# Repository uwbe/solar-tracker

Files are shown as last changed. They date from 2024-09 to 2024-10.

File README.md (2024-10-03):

# SolarTracker from Zachi Zolar
## Introduction
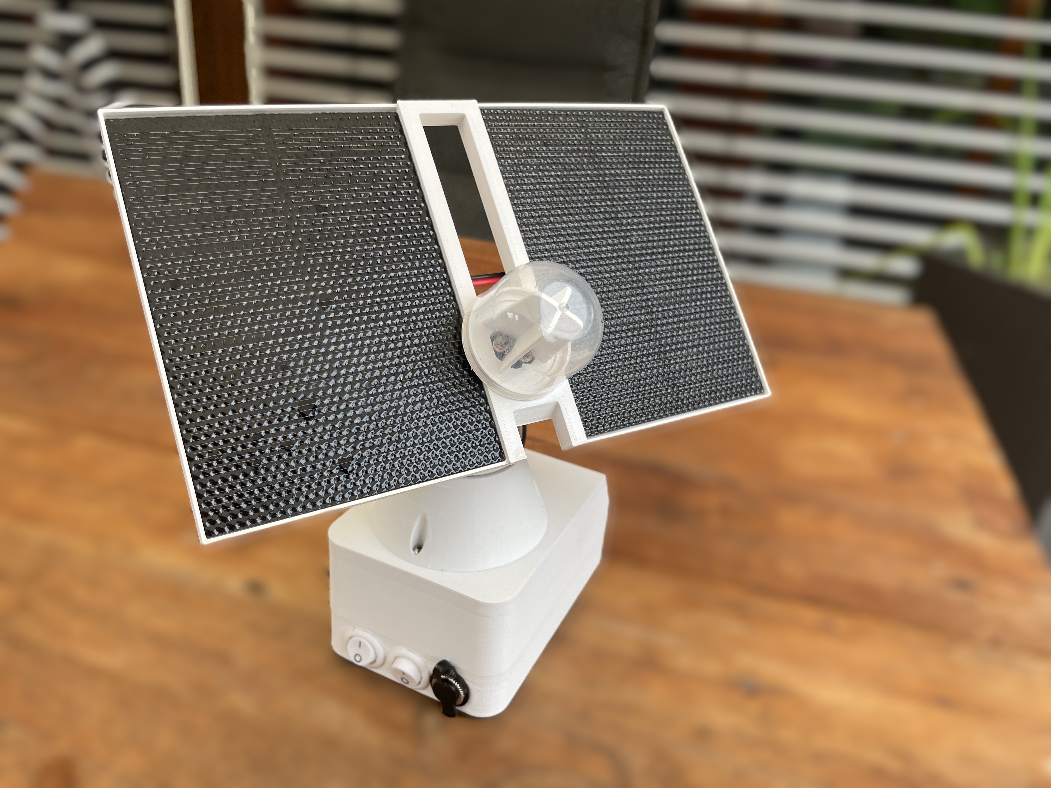
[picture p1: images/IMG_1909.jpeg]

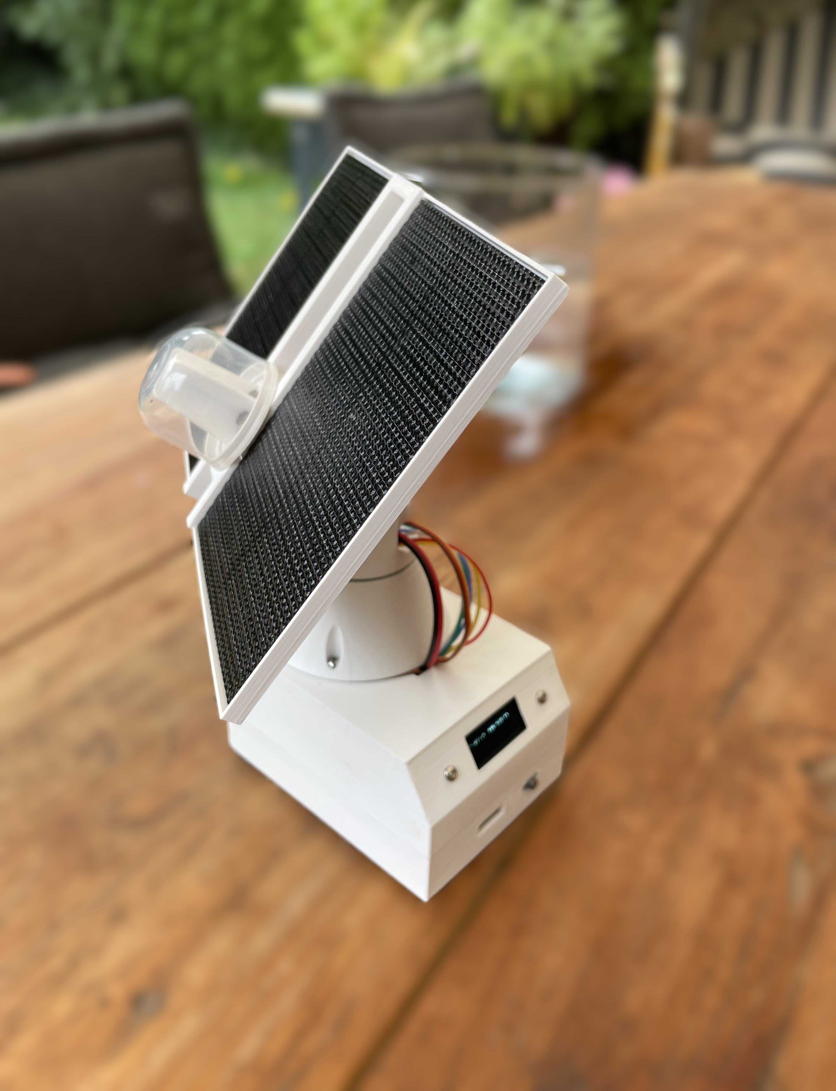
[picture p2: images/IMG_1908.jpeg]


This repository contains all necessary information to rebuilt a little solar tracker with 2x1W solar panels, which produces enough power to drive itself and, if the sun light is bright enough, a little garden fontain (1.4W).
The project is supposed as a starting point for Arduino enthusiast to create a funny little device and learn to bring all skills together, such as: 
* Programming Arduino Nano
* CAD
* PCB's and soldering
* 3D printing
* crimping wires and connections
* to overcome frustration
* to learn to pursue a goal patiently and persistently

The SolarTracker v1.0 from Zachi Zolar is far away from being ready. E.g. the first version was melting in the sun because it was 3D printed with PLA. This version printed with ASA withstands UV light and heat, 
but it is not really water protected.
Happy assembling!

A little [introduction](https://www.youtube.com/watch?v=XpIjK1iY8B4&t=24s) video in German on Youtube.

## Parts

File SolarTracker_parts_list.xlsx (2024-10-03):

Part | Amount | Example Order
Arduino Nano | 1 | https://de.aliexpress.com/item/1005005967644175.html
JST 2,54 15pin male | 2 | https://de.aliexpress.com/item/1005005258694395.html?scm_id=1007.40050.354490.0&scm-url=1007.40050.354490.0
JST 2,54 15pin female | 2 | https://de.aliexpress.com/item/4001198421663.html
Oled Display 0.91" | 1 | https://de.aliexpress.com/item/1005006365875553.html
Resistor 10k | 4 | https://de.aliexpress.com/item/32315929780.html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
photo resitor (LDR) | 4 | https://de.aliexpress.com/item/1005005968714360.html
Switch on/off | 2 | https://de.aliexpress.com/item/4000904999665.html
Clinch socket | 1 | https://de.aliexpress.com/item/1005005191616601.html
Clinch plug | 1 | https://de.aliexpress.com/item/1005001689451761.html
Servo SG90 | 2 | https://de.aliexpress.com/item/1005006283358420.html
Solar-Panel 1W | 2 | https://www.amazon.de/dp/B0BJPXJ61X?ref=ppx_yo2ov_dt_b_fed_asin_title
Dupont angled 90° 5pin | 1 | https://de.aliexpress.com/item/1005006438592096.html
Dupont pin header male 7pin | 1
Dupont pin header male 4pin | 1
Dupont pin header male 2pin | 1
INA219 | 1 | https://de.aliexpress.com/item/32377617416.html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
Akku 3.7V 14500 | 1 | https://de.aliexpress.com/item/1005004570483188.html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
Solar-Power Manager Waveshare SKU: 16120 | 1 | https://de.aliexpress.com/item/1005007342760815.html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
Brass Embedment Knurled Nut Heat Set | 1 | https://de.aliexpress.com/item/1005006359548769.html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
Stainless Steel Precision Ball set | 1 | https://de.aliexpress.com/item/1005005478220120.html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
JST Female Housing 4pins | 1 | https://www.amazon.de/dp/B0BHT1FQGY?ref=ppx_yo2ov_dt_b_fed_asin_title
Mini garden fontain max. 2.5 W | 1 | https://www.amazon.de/dp/B09V7RVX99?ref=ppx_yo2ov_dt_b_fed_asin_title
laboratory circuit board | 2 | https://de.aliexpress.com/item/1005007538599139.html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
3D printed parts from the STL directory | 10
PCB's as described in fritzing (or laboratory circuit boards) | 2
M3 and M2.5 Screws | various | https://www.amazon.de/dp/B0BQ7GGZ9M?ref=ppx_yo2ov_dt_b_fed_asin_title
Wires |  | https://www.amazon.de/dp/B098JKC4HW?ref=ppx_yo2ov_dt_b_fed_asin_title
ASA Filament | 1 | https://www.amazon.de/dp/B0C5H7S96Y?ref=ppx_yo2ov_dt_b_fed_asin_title
cover cap of Rituals of Hammam | 1 | https://www.amazon.de/RITUALS-Duschschaum-Vorteilspaket-Das-Ritual-Hammam/dp/B0CL4SBDPQ?hvadid=696322103951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
Aihasd 30 Stück Screw Terminal Leiterplatten-Anschlussklemme Block 5.08mm 2 Pin Pitch Klemme Printklemme 300V 16A | 1 | https://www.amazon.de/dp/B00VGGFPZW?ref=ppx_yo2ov_dt_b_fed_asin_title

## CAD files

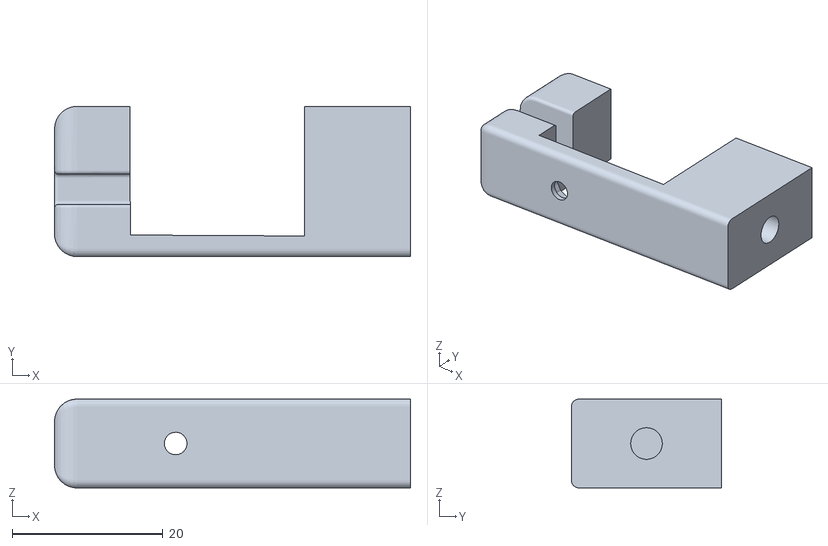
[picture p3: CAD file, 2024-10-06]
stl/solar_arm_big_sg90.stl
47.3 x 19.9 x 11.8

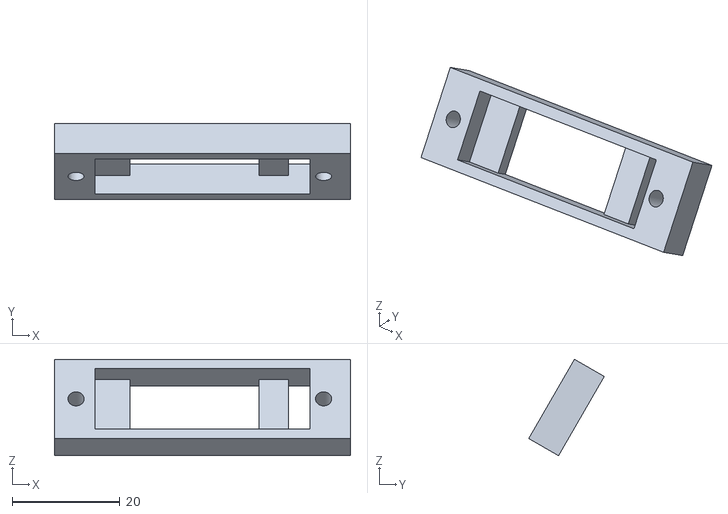
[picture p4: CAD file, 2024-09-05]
stl/solar_display.stl
55.0 x 14.0 x 17.9

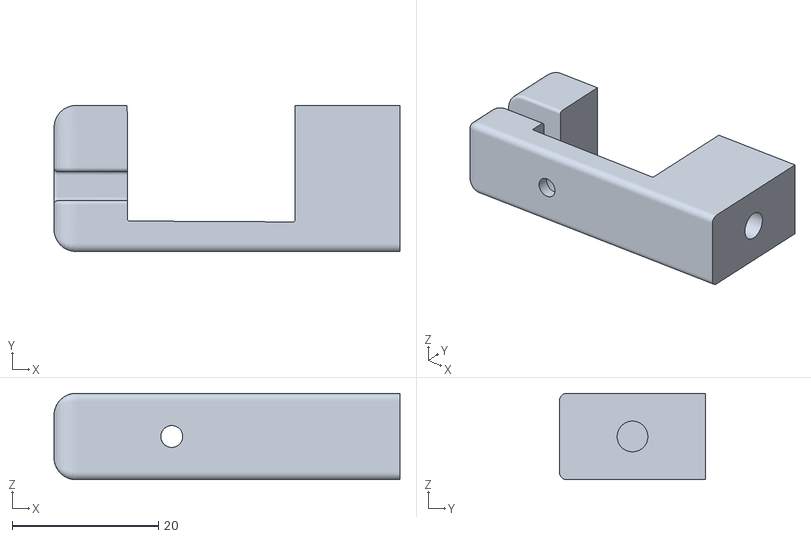
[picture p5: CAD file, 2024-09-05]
stl/solar_arm.stl
47.3 x 19.9 x 11.8

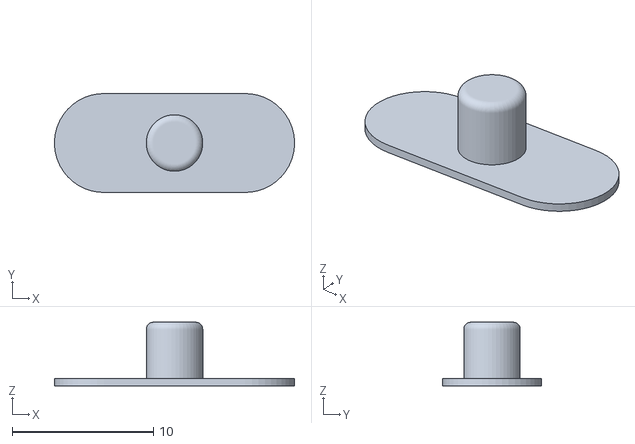
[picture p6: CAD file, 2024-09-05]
stl/solar_switch_cover.stl
17.0 x 7.00 x 4.50

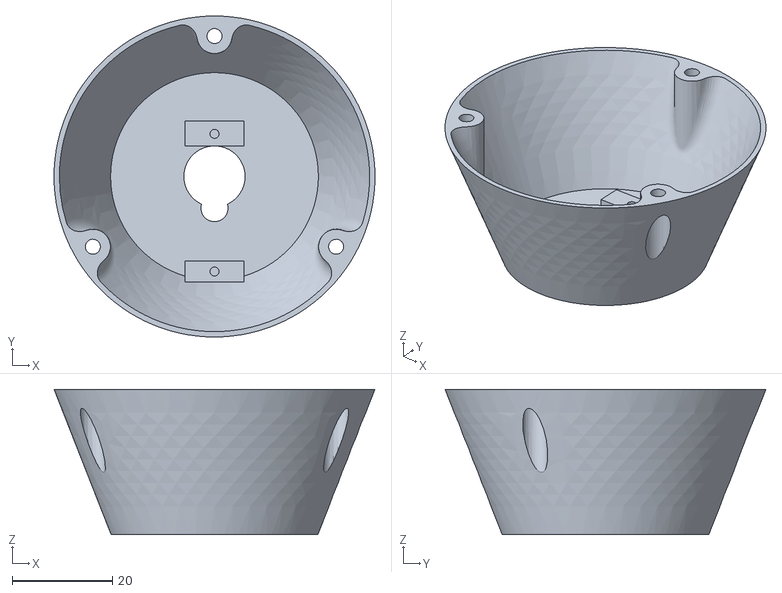
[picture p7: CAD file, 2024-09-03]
stl/solar_cone_base.stl
64.0 x 64.0 x 29.0

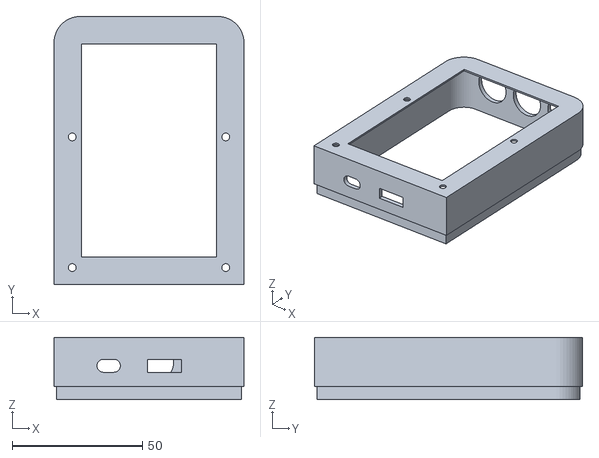
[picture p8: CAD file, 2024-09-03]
stl/solar_power_pack_v2.stl
73.0 x 103.0 x 24.0

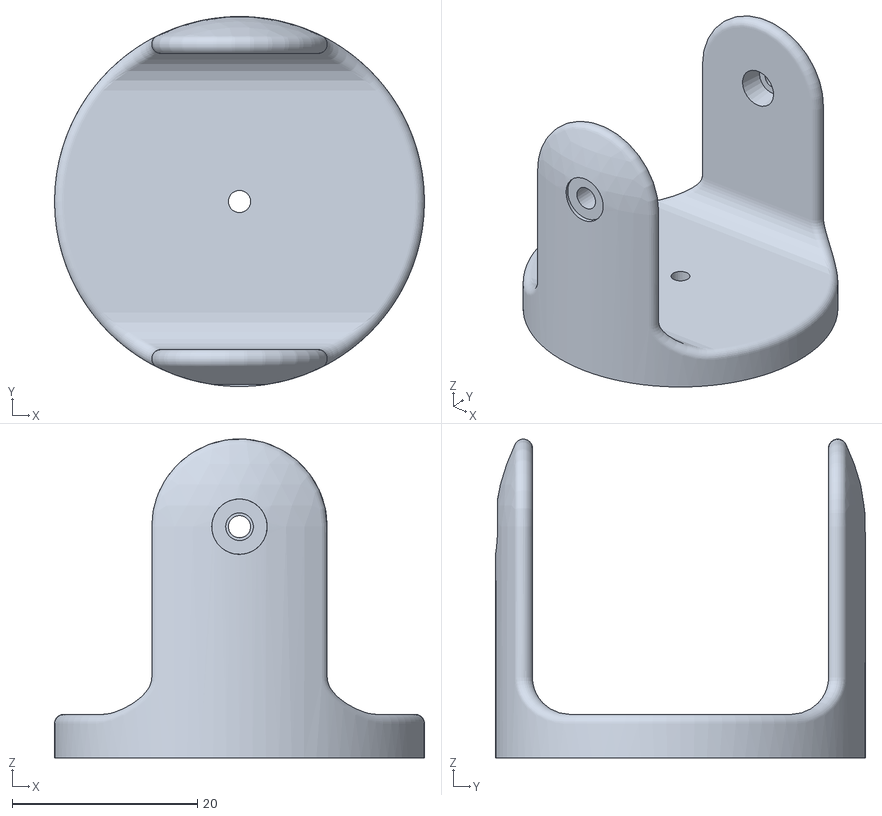
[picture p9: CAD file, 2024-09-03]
stl/solar_head.stl
40.0 x 40.0 x 34.5

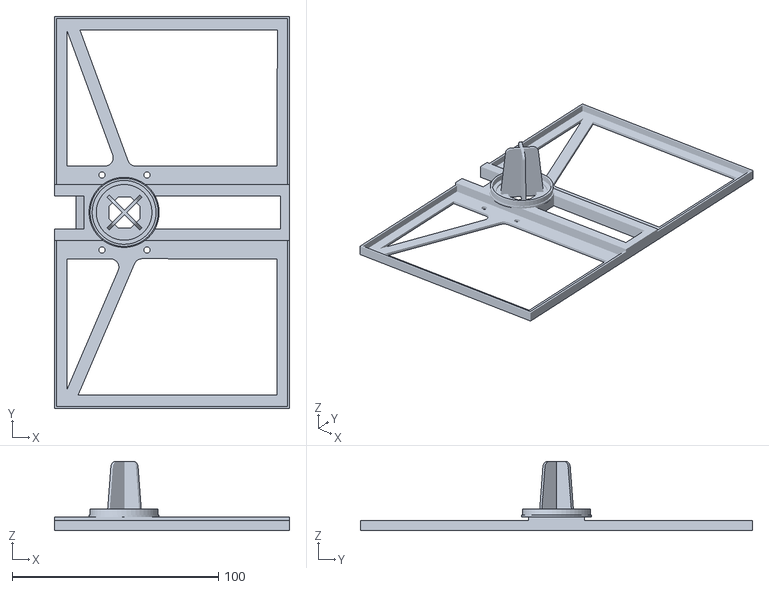
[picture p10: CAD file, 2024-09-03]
stl/solar_ldr_2W_panel.stl
113.8 x 190.0 x 33.5

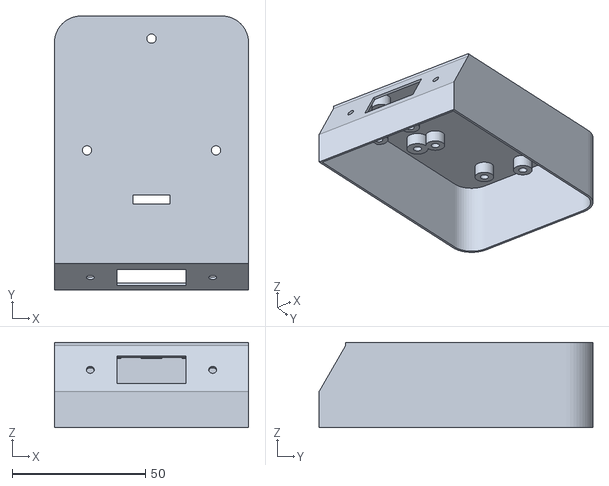
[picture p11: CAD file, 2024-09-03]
stl/solar_body_v2.stl
73.0 x 103.0 x 32.0

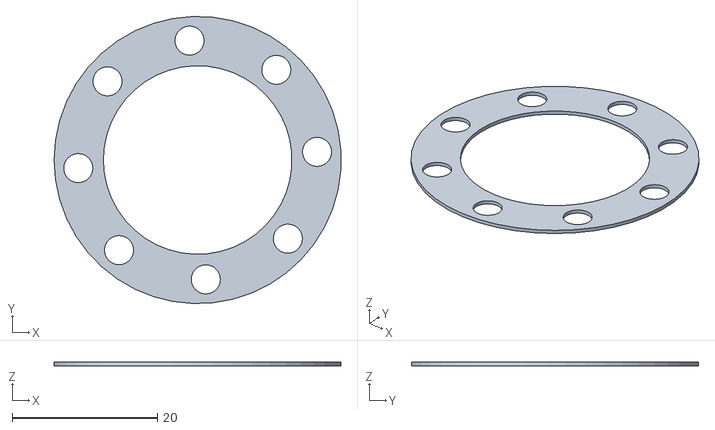
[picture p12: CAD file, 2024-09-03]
stl/solar_bearing.stl
39.6 x 39.6 x 0.5

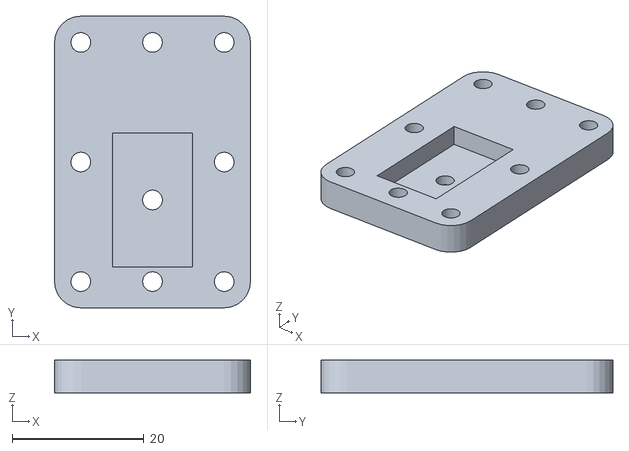
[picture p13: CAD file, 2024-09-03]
stl/solar_support.stl
29.8 x 44.4 x 5.00

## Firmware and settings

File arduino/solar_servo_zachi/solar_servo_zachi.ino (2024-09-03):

#include <Servo.h>
#include <Wire.h>
#include <Adafruit_GFX.h>
#include <Adafruit_SSD1306.h>
#include <Adafruit_INA219.h>

//0x31
#define OLED_RESET -1
#define SCREEN_WIDTH 128 // OLED display width, in pixels
#define SCREEN_HEIGHT 32 // OLED display height, in pixels
Adafruit_SSD1306 display(OLED_RESET);
bool invert = true;

Adafruit_INA219 ina219;

Servo horizontal; // horizontal servo
int servoh = 90;
int servohLimitHigh = 180;
int servohLimitLow = 0;

Servo vertical; // vertical servo
int servov = 45;
int servovLimitHigh = 95;
int servovLimitLow = 0;

// LDR pin connections
// name = analogpin;
int ldrtop = A0; //LDR top
int ldrright = A3; //LDR rigt
int ldrbottom = A1; //LDR bottom
int ldrleft = A2; //LDR left
int tolerance = 10;
int top = 0;
int bottom = 0;
int left = 0;
int right = 0;

int xpos = 89;
int dir = -1;

bool isSleepMode = false;
unsigned long startMillis;  
long currentAvg = 0;

//INA219 variables
float shuntvoltage = 0;
  float busvoltage = 0;
  float current_mA = 0;
  float loadvoltage = 0;
  float power_mW = 0;

static const unsigned char PROGMEM sun [] = {
0x80, 0x00, 0x00, 0x00, 0x00, 0x00, 0x00, 0x00, 0x43, 0xFF, 0xFF, 0xFF, 0xFF, 0xFF, 0xFF, 0x80,
0x40, 0x00, 0x00, 0x00, 0x00, 0x00, 0x00, 0x00, 0x80, 0x00, 0x00, 0x00, 0x00, 0x00, 0x00, 0x00,
0x40, 0x00, 0x00, 0x00, 0x00, 0x00, 0x00, 0x00, 0x80, 0x00, 0x00, 0x00, 0x00, 0x00, 0x00, 0x00,
0x20, 0x00, 0x00, 0x00, 0x00, 0x00, 0x00, 0x01, 0x02, 0x00, 0x00, 0x00, 0x00, 0x00, 0x00, 0x00,
0x20, 0x00, 0x00, 0x00, 0x00, 0x00, 0x00, 0x01, 0x01, 0xE0, 0x00, 0x00, 0x00, 0x00, 0x00, 0x00,
0x10, 0x00, 0x00, 0x00, 0x00, 0x00, 0x00, 0x02, 0x00, 0x1E, 0x00, 0x00, 0x00, 0x00, 0x00, 0x00,
0x08, 0x00, 0x00, 0x00, 0x00, 0x00, 0x00, 0x04, 0x00, 0x01, 0xE0, 0x00, 0x00, 0x00, 0x00, 0x00,
0x04, 0x00, 0x00, 0x00, 0x00, 0x00, 0x00, 0x08, 0x00, 0x00, 0x1C, 0x00, 0x00, 0x00, 0x00, 0x00,
0x02, 0x00, 0x00, 0x00, 0x00, 0x00, 0x00, 0x10, 0x18, 0x00, 0x00, 0x00, 0x00, 0x00, 0x00, 0x00,
0x02, 0x00, 0x00, 0x00, 0x00, 0x00, 0x00, 0x10, 0x06, 0x00, 0x00, 0x00, 0x00, 0x00, 0x00, 0x00,
0x01, 0x80, 0x00, 0x00, 0x00, 0x00, 0x00, 0x60, 0x01, 0x80, 0x00, 0x00, 0x00, 0x00, 0x00, 0x00,
0x40, 0x40, 0x00, 0x00, 0x00, 0x00, 0x00, 0x80, 0x00, 0x40, 0x00, 0x00, 0x00, 0x00, 0x00, 0x00,
0x80, 0x20, 0x00, 0x00, 0x00, 0x00, 0x01, 0x00, 0x00, 0x30, 0x00, 0x00, 0x00, 0x00, 0x00, 0x00,
0x00, 0x10, 0x00, 0x00, 0x00, 0x00, 0x02, 0x00, 0x80, 0x0C, 0x00, 0x00, 0x00, 0x00, 0x00, 0x00,
0x00, 0x0C, 0x00, 0x00, 0x00, 0x00, 0x0C, 0x00, 0x40, 0x03, 0x00, 0x00, 0x00, 0x00, 0x00, 0x00,
0x00, 0x03, 0x00, 0x00, 0x00, 0x00, 0x30, 0x00, 0x20, 0x00, 0x80, 0x00, 0x00, 0x00, 0x00, 0x00,
0x02, 0x00, 0xC0, 0x00, 0x00, 0x00, 0xC0, 0x10, 0x10, 0x00, 0x60, 0x00, 0x00, 0x00, 0x00, 0x00,
0x04, 0x00, 0x30, 0x00, 0x00, 0x03, 0x00, 0x08, 0x08, 0x00, 0x18, 0x00, 0x00, 0x00, 0x00, 0x00,
0x04, 0x00, 0x0E, 0x00, 0x00, 0x1C, 0x00, 0x04, 0x04, 0x00, 0x06, 0x00, 0x00, 0x00, 0x00, 0x00,
0x08, 0x00, 0x01, 0xF0, 0x01, 0xE0, 0x01, 0x02, 0x02, 0x00, 0x01, 0x80, 0x00, 0x00, 0x00, 0x00,
0x10, 0x08, 0x00, 0x0F, 0xFE, 0x00, 0x01, 0x01, 0x01, 0x00, 0x00, 0x40, 0x00, 0x00, 0x00, 0x00,
0x20, 0x10, 0x00, 0x00, 0x00, 0x00, 0x00, 0x80, 0x80, 0x80, 0x00, 0x30, 0x00, 0x00, 0x00, 0x00,
0x40, 0x10, 0x40, 0x00, 0x00, 0x00, 0x00, 0x80, 0x00, 0x40, 0x00, 0x0C, 0x00, 0x00, 0x00, 0x00,
0x40, 0x20, 0x80, 0x00, 0x00, 0x00, 0x40, 0x40, 0x00, 0x20, 0x00, 0x03, 0x00, 0x00, 0x00, 0x00,
0x80, 0x40, 0x80, 0x40, 0x00, 0x80, 0x40, 0x20, 0x00, 0x10, 0x00, 0x00, 0x80, 0x00, 0x00, 0x00,
0x00, 0x01, 0x00, 0x80, 0x80, 0x40, 0x20, 0x20, 0x00, 0x08, 0x00, 0x00, 0x60, 0x00, 0x00, 0x00,
0x00, 0x01, 0x00, 0x80, 0x80, 0x40, 0x20, 0x10, 0x00, 0x04, 0x00, 0x00, 0x18, 0x00, 0x00, 0x00,
0x00, 0x02, 0x01, 0x00, 0x80, 0x40, 0x10, 0x10, 0x00, 0x02, 0x00, 0x00, 0x06, 0x00, 0x00, 0x00,
0x00, 0x04, 0x01, 0x00, 0x80, 0x20, 0x10, 0x08, 0x00, 0x01, 0x00, 0x00, 0x01, 0x00, 0x00, 0x00,
0x00, 0x04, 0x02, 0x00, 0x80, 0x20, 0x08, 0x04, 0x00, 0x00, 0x80, 0x00, 0x00, 0x00, 0x00, 0x00,
0x00, 0x08, 0x00, 0x00, 0x80, 0x20, 0x08, 0x04, 0x00, 0x00, 0x00, 0x00, 0x00, 0x00, 0x00, 0x00,
0x00, 0x10, 0x00, 0x00, 0x80, 0x10, 0x08, 0x02, 0x00, 0x00, 0x00, 0x00, 0x00, 0x00, 0x00, 0x00
};

static const unsigned char PROGMEM lupe_bmp[] = {
0x07, 0xc0, 0x00, 
0x18, 0x30, 0x00, 
0x20, 0x08, 0x00, 
0x40, 0x04, 0x00, 
0x40, 0x04, 0x00, 
0x80, 0x02, 0x00, 
0x80, 0x02, 0x00, 
0x80, 0x02, 0x00, 
0x80, 0x02, 0x00, 
0x80, 0x02, 0x00, 
0x40, 0x04, 0x00, 
0x40, 0x04, 0x00, 
0x20, 0x0c, 0x00, 
0x18, 0x3e, 0x00, 
0x07, 0xc7, 0x00, 
0x00, 0x03, 0x80, 
0x00, 0x01, 0xc0, 
0x00, 0x00, 0xe0, 
0x00, 0x00, 0x70, 
0x00, 0x00, 0x30
};

static const unsigned char PROGMEM dark [] = {
0x00, 0x00, 0x00, 0x00, 0x20, 0x00, 0x00, 0x00, 0x00, 0x00, 0x00, 0x00, 0x00, 0x00, 0x00, 0x00,
0x00, 0x40, 0x00, 0x00, 0x20, 0x00, 0x00, 0x00, 0x0F, 0x78, 0x00, 0x00, 0x03, 0xF1, 0xFC, 0x00,
0x00, 0x40, 0x00, 0x00, 0x50, 0x00, 0x00, 0x01, 0xF0, 0x84, 0x00, 0x3F, 0xFC, 0x0E, 0x03, 0x00,
0x00, 0xA0, 0x00, 0x00, 0xDC, 0x00, 0x00, 0x7E, 0x10, 0x06, 0xFF, 0x40, 0x30, 0x08, 0x00, 0x80,
0x00, 0xA0, 0x00, 0x07, 0x03, 0x00, 0x00, 0x80, 0x00, 0x07, 0x00, 0xC0, 0x00, 0x00, 0x00, 0xF0,
0x07, 0x1C, 0x00, 0x01, 0xDC, 0x00, 0x01, 0x00, 0x00, 0x08, 0x00, 0x00, 0x00, 0x00, 0x00, 0x08,
0x18, 0x03, 0x00, 0x00, 0x50, 0x00, 0x01, 0x00, 0x00, 0x10, 0x00, 0x00, 0x00, 0x00, 0x00, 0x04,
0x07, 0x1C, 0x00, 0x00, 0x20, 0x00, 0x07, 0x00, 0x00, 0x10, 0x00, 0x00, 0x00, 0x00, 0x00, 0x04,
0x00, 0xA0, 0x00, 0x00, 0x20, 0x00, 0x08, 0x00, 0x01, 0xF0, 0x00, 0x00, 0x00, 0x00, 0x00, 0x0C,
0x00, 0xA0, 0x20, 0x00, 0x00, 0x00, 0x08, 0x00, 0x02, 0x00, 0x00, 0x00, 0x00, 0x00, 0x00, 0x1C,
0x00, 0x40, 0x20, 0x00, 0x00, 0x00, 0x08, 0x00, 0x04, 0x00, 0x00, 0x00, 0x00, 0x00, 0x00, 0x02,
0x00, 0x40, 0x50, 0x00, 0x00, 0x00, 0x06, 0x00, 0x04, 0x00, 0x00, 0x00, 0x00, 0x00, 0x00, 0x02,
0x00, 0x00, 0x50, 0x00, 0x00, 0x40, 0x04, 0x00, 0x03, 0x00, 0x00, 0x00, 0x00, 0x00, 0x1C, 0x02,
0x00, 0x03, 0x8E, 0x00, 0x00, 0x40, 0x04, 0x00, 0x00, 0x80, 0x00, 0x00, 0x00, 0x00, 0x02, 0x0C,
0x00, 0x0C, 0x01, 0x80, 0x00, 0xA0, 0x06, 0x00, 0x01, 0x00, 0x00, 0x00, 0x00, 0x00, 0x01, 0xF0,
0x00, 0x03, 0x8E, 0x00, 0x00, 0xA0, 0x01, 0xC0, 0x01, 0x00, 0x00, 0x00, 0x00, 0x00, 0x01, 0x00,
0x00, 0x00, 0x50, 0x00, 0x07, 0x1C, 0x00, 0xC1, 0x01, 0xF0, 0x00, 0x00, 0x00, 0x00, 0x02, 0x00,
0x00, 0x00, 0x50, 0x00, 0x18, 0x03, 0x00, 0x7F, 0x82, 0x7F, 0x00, 0x00, 0x00, 0x08, 0x0C, 0x00,
0x00, 0x00, 0x20, 0x00, 0x07, 0x1C, 0x00, 0x00, 0x7C, 0x06, 0x00, 0x00, 0x00, 0x1F, 0xF0, 0x00,
0x00, 0x00, 0x20, 0x00, 0x00, 0xA0, 0x00, 0x00, 0x00, 0x01, 0xE1, 0xF8, 0x00, 0x30, 0x00, 0x00,
0x00, 0x00, 0x00, 0x00, 0x00, 0xA0, 0x00, 0x00, 0x00, 0x00, 0x1E, 0x07, 0x03, 0xC0, 0x00, 0x00,
0x00, 0x00, 0x00, 0x00, 0x00, 0x40, 0x00, 0x00, 0x00, 0x00, 0x00, 0x00, 0xFC, 0x00, 0x00, 0x00,
0x00, 0x00, 0x00, 0x00, 0x00, 0x40, 0x00, 0x00, 0x00, 0x00, 0x00, 0x00, 0x00, 0x00, 0x00, 0x00,
0x00, 0x00, 0x00, 0x00, 0x00, 0x00, 0x00, 0x00, 0x00, 0x00, 0x00, 0x00, 0x00, 0x00, 0x00, 0x00,
0x00, 0x00, 0x00, 0x00, 0x00, 0x00, 0x00, 0x00, 0x00, 0x00, 0x00, 0x00, 0x00, 0x00, 0x00, 0x00,
0x00, 0x00, 0x00, 0x00, 0x00, 0x00, 0x00, 0x00, 0x00, 0x00, 0x00, 0x00, 0x00, 0x00, 0x00, 0x00,
0x00, 0x00, 0x00, 0x00, 0x00, 0x00, 0x00, 0x00, 0x00, 0x00, 0x00, 0x00, 0x00, 0x00, 0x00, 0x00,
0x00, 0x00, 0x00, 0x00, 0x00, 0x00, 0x00, 0x00, 0x00, 0x00, 0x00, 0x00, 0x00, 0x00, 0x00, 0x00,
0x00, 0x00, 0x00, 0x00, 0x00, 0x00, 0x00, 0x00, 0x00, 0x00, 0x00, 0x00, 0x00, 0x00, 0x00, 0x00,
0x00, 0x00, 0x00, 0x00, 0x00, 0x00, 0x00, 0x00, 0x00, 0x00, 0x00, 0x00, 0x00, 0x00, 0x00, 0x00,
0x00, 0x00, 0x00, 0x00, 0x00, 0x00, 0x00, 0x00, 0x00, 0x00, 0x00, 0x00, 0x00, 0x00, 0x00, 0x00,
0x00, 0x00, 0x00, 0x00, 0x00, 0x00, 0x00, 0x00, 0x00, 0x00, 0x00, 0x00, 0x00, 0x00, 0x00, 0x00
};


void setup() {
  Serial.begin(9600);
  display.begin(SSD1306_SWITCHCAPVCC, 0x3C);
  display.setTextSize(1);
  display.setTextColor(WHITE);
  splashScreen();
  ina219.begin();
  pinMode (ldrtop, INPUT);                                  // Config the mocrocontroller pins as an input pins.
  pinMode (ldrright, INPUT);
  pinMode (ldrbottom, INPUT);
  pinMode (ldrleft, INPUT);
  horizontal.attach(2);
  vertical.attach(3);
  vertical.write(servov);
  delay(1000);
  horizontal.write(servoh);
  delay(500);
  startMillis = millis();
}

void loop() {
  top = analogRead(ldrtop);
  right = analogRead(ldrright);
  left = analogRead(ldrleft);
  bottom = analogRead(ldrbottom);
  readINA219();
  
  if (isToDark() && millis() - startMillis  > 10000) {
    sleepMode();
    logSerial();
    return;
  } else {
    if (isSleepMode) {
      wakeUp();
    }
  }
  logSerial();
  if (inRange()){
    info();
  } else {
    //info();
    searchScreen();
  }
  verticalMove();
  horizontalMove();
  delay(500);
}

void horizontalMove() {
  if (abs(left - right) < tolerance) return;
  if (left < right)
  {
    servoh = --servoh;
    if (servoh <= servohLimitLow)
    {
      servoh = servohLimitLow;
      Serial.println("max east!");
    }
  }
  else if (left > right)
  {
    servoh = ++servoh;
    if (servoh > servohLimitHigh)
    {
      Serial.println("max west!");
      servoh = servohLimitHigh;
    }
  }
  else if (left = right)
  {
    delay(800);
  }
  horizontal.write(servoh);
}

void verticalMove() {
  if (abs(top - bottom) < tolerance) return;
  if (top > bottom) {
    servov = ++servov;
    if (servov > servovLimitHigh) {
      Serial.print("max height!: ");
      Serial.println(servov);
      servov = servovLimitHigh;
    }
  }
  else if (top < bottom) {
    servov = --servov;
    if (servov < servovLimitLow) {
      servov = servovLimitLow;
      Serial.println("min height!");
    }
  }
  vertical.write(servov);
}

bool inRange() {
  return abs(top - bottom) < tolerance * 3 && abs(left - right) < tolerance * 3;
}

bool isToDark() {
  currentAvg = (top + bottom + left + right) / 4;
  return currentAvg < 200; 
}

void sleepMode() {
  if (!isSleepMode) {
    servov = 85;
    vertical.write(servov);
  }
  isSleepMode = true;
  darkScreen();
}

void wakeUp() {
  isSleepMode = false;
  servov = 45;
  vertical.write(servov);
}

void readINA219() {
  shuntvoltage = ina219.getShuntVoltage_mV();
  busvoltage = ina219.getBusVoltage_V();
  current_mA = ina219.getCurrent_mA();
  power_mW = ina219.getPower_mW();
  loadvoltage = busvoltage + (shuntvoltage / 1000);
}

void logSerial() {
  Serial.print("top/bottom: ");
  Serial.print(top);
  Serial.print("/");
  Serial.print(bottom);
  Serial.print("/");
  Serial.println(abs(top - bottom));
  Serial.print("right/left: ");
  Serial.print(right);
  Serial.print("/");
  Serial.print(left);
  Serial.print("/");
  Serial.println(abs(left - right));
  Serial.println("");
  Serial.print("Bus Voltage:   "); Serial.print(busvoltage); Serial.println(" V");
  Serial.print("Shunt Voltage: "); Serial.print(shuntvoltage); Serial.println(" mV");
  Serial.print("Load Voltage:  "); Serial.print(loadvoltage); Serial.println(" V");
  Serial.print("Current:       "); Serial.print(current_mA); Serial.println(" mA");
  Serial.print("Power:         "); Serial.print(power_mW); Serial.println(" mW");
  Serial.println();
}

void info() {
  display.clearDisplay();
  display.setCursor(0,0);
  //display.println("     Zachi Zolar");
  display.print("ob/unt/d: ");
  display.print(top);
  display.print("/");
  display.print(bottom);
  display.print("/");
  display.println(abs(top - bottom));
  display.print("re/li/d:  ");
  display.print(right);
  display.print("/");
  display.print(left);
  display.print("/");
  display.println(abs(left - right));
  display.print("pos h/v:  ");
  display.print(servoh);
  display.print(" - ");
  display.println(servov);
  display.print("mW/mA: ");
  display.print(power_mW);
  display.print("/");
  display.print(current_mA);
  display.display();
}

void splashScreen() {
  display.clearDisplay();
  display.drawBitmap(0, 0,  sun, 128, 32, WHITE);
  display.setCursor(20,1);
  display.print("Zachi");
  display.setCursor(91,7);
  display.print("Zolar");
  display.display();
}

void searchScreen() {
  if (xpos > 100 || xpos < 5) {
    dir = dir * -1;
  }
  xpos = xpos + dir * 2;
  display.clearDisplay();
  display.drawBitmap(0, 0,  sun, 128, 32, WHITE);
  display.drawBitmap(xpos, 12,  lupe_bmp, 20, 20, WHITE);
  display.setCursor(20,1);
  display.print("Suche");
  display.display();
}

void darkScreen() {
  if (xpos > 90 || xpos < 5) {
    dir = dir * -1;
  }
  xpos = xpos + dir * 2;
  display.clearDisplay();
  display.drawBitmap(0, 0,  dark, 128, 32, WHITE);
  display.setCursor(xpos,24);
  display.print("Snooze");
  display.setCursor(88, 7);
  display.print(currentAvg);
  display.display();
}

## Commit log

2024-09-03 Add files initially
    [LDR Array-v1.fzz, SolarTracker-v1.fzz]
2024-09-03 Add stl files initially
    [solar_bearing.stl, solar_body_v2.stl, solar_cone_base.stl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]
2024-09-05 Add parts list initially
    [SolarTracker_parts_list.xlsx]
2024-09-05 Add cover cap to parts list
    [SolarTracker_parts_list.xlsx]
2024-10-03 Add screw terminal to parts list
    [SolarTracker_parts_list.xlsx]
2024-10-06 V2 - get power for the servos directly from the power supply not from the Ardiuno 5v pin SG90 - new set of SG90 servos has different dimensions - add modified arm CAD/STL files
    [SolarTracker-v2.fzz, solar_arm_big_sg90.stl]
